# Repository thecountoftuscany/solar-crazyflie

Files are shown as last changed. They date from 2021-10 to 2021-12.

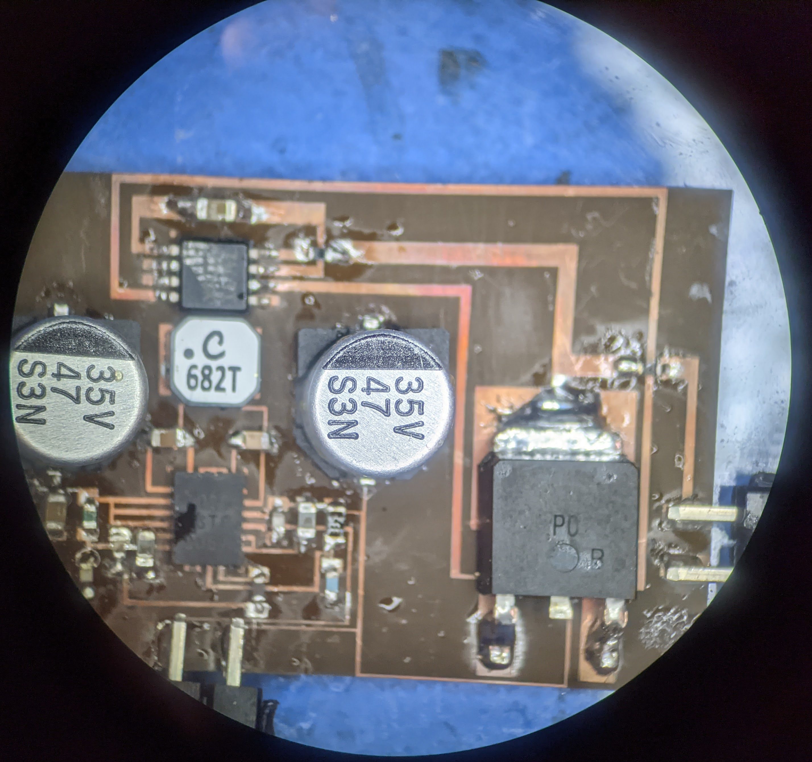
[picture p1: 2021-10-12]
resources/ckt_cropped.jpg

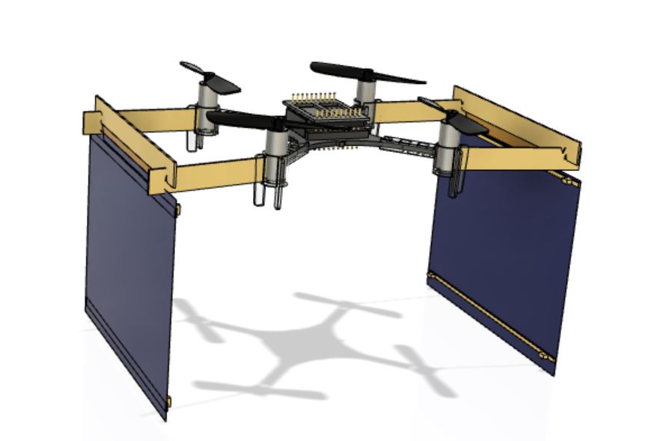
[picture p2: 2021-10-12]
resources/solar-panels-retracted.JPG

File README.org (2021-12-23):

#+title: Toward battery-free flight: Duty cycled recharging of small drones (IEEE IROS 2021)
#+author: Nishant Elkunchwar, Suvesha Chandrasekaran, Vikram Iyer, Sawyer B. Fuller

This repository contains the source code and circuit schematics used in the IEEE IROS 2021 paper titled [[https://ieeexplore.ieee.org/document/9636087][Toward battery-free flight: Duty cycled recharging of small drones]].
#+html: <p align="center"><img src="resources/drone.JPG" alt="The drone carrying the thin film solar panels and all other components" width="500" /></p>

* Major highlights
** A solar charging circuit
#+html: <p align="center"><img src="resources/ckt_cropped.jpg" alt="Solar charging circuit" width="500" /></p>
- 39 x 21 mm, 1.83 g circuit laser etched using a DPSS laser machine
- 90.84 % average efficiency across different light intensities (see the [[Results]] section)
- charges a 250 mAh 1S LiPo battery completely with two 94 x 73 mm (1.98 g each) thin film flexible solar panels in 3 hr 3 min (see the [[Results]] section) in real outdoor lighting varying due to intermittent clouds
** A passive folding mounting mechanism
https://user-images.githubusercontent.com/14308382/136243970-1dca0429-ac65-4f95-9dc4-829e8c846ea5.mp4
- fabricated using 2.3 mm balsa wood, weighs just 0.83 g
- enables airflow from propellers for lift, decreases destabilizing torques
- uses gravity for folding down and ground effect (increase in air pressure below the drone near the ground) to open out the panels; passive mechanism implies no actuators, making it simple, effective and light
** A landing site selection strategy
https://user-images.githubusercontent.com/14308382/136245977-f141101d-2a0c-4fd0-a3ba-4daf73d85fbe.mov
- detects presence of light to avoid landing in shaded regions
- avoids crashing into nearby obstacles
- avoids landing in unflat terrain where panels cannot open out for recharging
* Description of repository contents
- [[./circuits][circuits]]: charging circuit schematics and vector drawings used for laser etching
- [[./data][data]]: all recorded experiment data used for generating all plots (see the [[Results]] section)
- [[./docs][docs]]: relevant datasheets etc
- [[./resources][resources]]: resources used in this README
- [[./scripts][scripts]]: all scripts
  - [[./scripts/plots][scripts/plots]]: the scripts used for generating all plots (see the [[Results]] section)
  - [[./scripts/controller.py][scripts/controller.py]]: script used to manually control the crazyflie and trigger the landing site selection sequence. Heavily borrows from [[https://github.com/thecountoftuscany/crazyflie-run-and-tumble/blob/master/scripts/cflibController.py][thecountoftuscany/crazyflie-run-and-tumble/scripts/cflibController.py]] for the keyboard control part.
    - While the battery is not low, the drone is controlled manually to fly around. This behaviour can be substituted with whatever persistent operations (autonomous or otherwise) are desired in a particular application.
    - To get outside a shaded area, the drone keeps moving forward (defined as at least 1000 lux for indoor light, and 100,000 lux for outdoors). This behaviour can be changed to a random walk or anything else as desired.
    - To avoid obstacles, the drone moves directly away from the closest one. This behaviour can be changed to turning away, wall-following, sliding mode controller or anything else as desired
    - On detecting an unflat area, the drone moves forward by a set amount to re-check for flatness. This behaviour can be changed to a random walk or anything else as desired
    - To check for flatness, the drone measures time of flight measurements while moving in a square around the area to be tested. This behaviour can be changed to a different trajectory (for eg. a circle) as desired.
  - [[./scripts/crazyflie-thrust-control.py][scripts/crazyflie-thrust-control.py]]: script used to control crazyflie's thrust (open loop, constant or closed loop, hovering) and save data for flight performance plots (see the [[Results]] section)
* Requirements
The following python packages (obtain using =pip=, =conda=, your OS distribution package manager or any other preferred means):
- =numpy=
- =pygame=
- [[https://github.com/bitcraze/crazyflie-lib-python][cflib]]
- =argparse=
- =matplotlib=
* Background
** UAV flight time limits persistent operations
- Battery capacity limits flight time: low energy density of currently available batteries, but high power required for hovering flight
- Miniaturization reduces required flight power and solar harvesting increases flight time
** Why solar power?
*** Scaling effects due to miniaturization
#+html: <p align="center"><img src="resources/mass_vs_array_scaling2.png" alt="PV cell size required for hovering reduces faster than drone size" width="500" /></p>
- Scaling effects lead to lower required hover power for smaller robots. This scales down faster than required photovoltaic panel size required for continuous hover (see figure).
- For scale l:
  + PV cell area scales as l^2
  + Required flight power for hovering scales as l^7/2
- From existing robots, we can see this trend that required PV cell size for continuous hovering becomes smaller than the robot size below approx 1 g robot mass. For robots slightly above this threshold duty cycled operation is possible: that is, the robot operates normally until the battery is low, at which point it stops, recharges its battery and continues operation indefinitely.
*** Simplicity: previous solutions too complicated for small aerial robots
+ Tethered flight: restricts drone movement
+ Wireless power transfer, autonomously docking to power outlets, hot-swapping UAV batteries in-flight: needs additional base stations or docks, bulky sensors (eg. cameras, lidars) to search for and align / dock with them, computationally intensive algorithms (eg. computer vision) for planning, and additional sensors for localization. Also restricts how far the drone can travel via dependence on these external systems
+ Solar-powered hovering for fixed wing drones: only achieved on large, fixed wing drones. Large size increases cost, use of unpackaged monocrystalline solar panels makes them fragile, and being fixed wing decreases agility and they cannot hover which limits their utility for many applications
In contrast, this system is simple, self-contained and deployable on size, weight, power and computationally limited platforms, specially, insect scale robots like the [[https://arxiv.org/pdf/2001.02320.pdf][UW Robofly]].
** Why duty cycled?
- Inspiration from IoT radios: low average power
- Continuous hover with only solar power not possible at this scale. Duty cycled operation enables indefinite operation without any human intervention or existence of any external power infrastructure.
- Traversal of long distances possible: no need for a return journey
* System
- 21 g palm-sized drone, Crazyflie 2.1 with optic flow deck, multiranger deck, and BH1750 light sensor (driver can be obtained [[https://github.com/thecountoftuscany/crazyflie-run-and-tumble/blob/master/crazyflie-firmware/src/deck/drivers/src/bh1750deck.c][here]])
- Custom charging circuit
#+html: <p align="center"><img src="resources/schematic.png" alt="Charging circuit schematic" width="500" /></p>
- Solar panels: two thin-film flexible, amorphous silicon cells (200 microns), 94 x 73 mm
* Results
** Solar charging
*** Complete battery charge
#+html: <p align="center"><img src="resources/charging-curve.png" alt="Solar charging a LiPo battery" width="500" /></p>
*** Charging efficiency
#+html: <p align="center"><img src="resources/efficiency.png" alt="Efficiency of charging circuit" width="400" /></p>
*** Charging times for different cell configurations
|----------------+----------+---------------------------------+----------------+---------------------|
| Panels         | Mass (g) | Avg light intensity (x10^3 lux) | Avg efficiency | Charging time (min) |
|----------------+----------+---------------------------------+----------------+---------------------|
| two MPT4.8-75  |     3.96 |                          107.16 |         90.84% |                 183 |
| four MPT4.8-75 |     7.92 |                           71.41 |         89.61% |                  84 |
| four MPT6-75   |     9.20 |                           65.74 |          86.94 |                  80 |
|----------------+----------+---------------------------------+----------------+---------------------|
** Folding solar panel mounts
#+html: <p align="center"><img src="resources/solar-panels-flat.png" alt="Battery discharge curves under different loads" width="320" /> <img src="resources/solar-panels-retracted.JPG" width="320"></p>
*** Necessity
- to allow airflow from propellers
- to reduce imbalancing torques
- to enable passive transition between states
*** Flight performance
- 4.7 min flight time
- can travel 400 m at maximum velocity in single discharge, or 1.2 km in a day (assuming two recharges which is typical in a day)
#+html: <p align="center"><img src="resources/discharging-curves.png" alt="Battery discharge curves under different loads" width="320" /></p>
** Landing site selection
#+html: <p align="center"><img src="resources/flatness-check-colored.png" alt="Landing site selection algorithm" width="800" /></p>
* Authors
For more details refer to the paper [[https://ieeexplore.ieee.org/document/9636087][here]]. You can also contact one of the authors below:
- [[https://students.washington.edu/nishante][Nishant Elkunchwar]]
- [[https://www.linkedin.com/in/suvesha-c][Suvesha Chandrasekaran]]
- [[https://homes.cs.washington.edu/~vsiyer/][Vikram Iyer]]
- [[https://faculty.washington.edu/minster/][Sawyer B. Fuller]]
* Acknowledgements
The authors would like to thank [[https://yogeshchukewad.com/][Yogesh Chukewad]] for insightful suggestions during the writing of the paper, and [[https://www.afrl.af.mil/AFOSR/][The Air Force Office of Scientific Research (AFOSR)]], grant no. FA9550-14-1-0398 by [[http://nifti.washington.edu/][The Air Force Center of Excellence on Nature-Inspired Flight Technologies and Ideas (NIFTI)]] for funding the equipment used in this research.

* Todos
- [ ] The crazyflie now has an [[https://www.bitcraze.io/documentation/repository/crazyflie-firmware/2020.02/app_layer/][app layer]]. Implement this algorithm on-board and remove the dependency on an external computer

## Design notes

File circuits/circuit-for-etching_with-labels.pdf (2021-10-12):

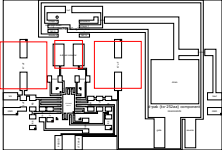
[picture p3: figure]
LTC3130; GND 21; BST1 1; PVIN 2; VIN 3; RUN 4; VCC 5; MPPC 6; GND 7; GND 8; ILIM 10; MODE 11; EXTVcc 12; PGOOD 13; VOUT 14; BST2 16; PGND 19; PGND 18; 6.8 uH inductor; Vin; GND; 0 ohm; Vout; PGOOD; LTC Vout; VCapL 1 Gate pull down 2 NC 3; Anode 4; Gate drive 6; VCapH 7; Cathode 8; d-pak (to-252aa) component; IRLR024NTR; drain; gate; source

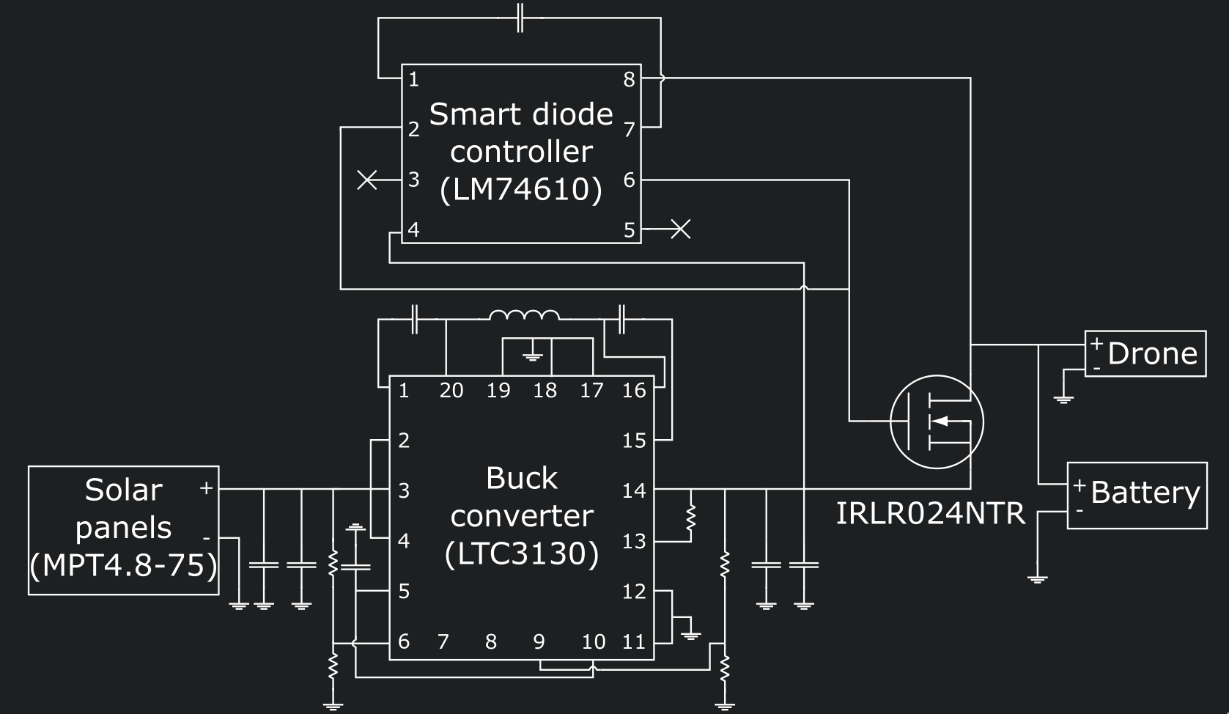
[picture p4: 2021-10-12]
resources/schematic.png

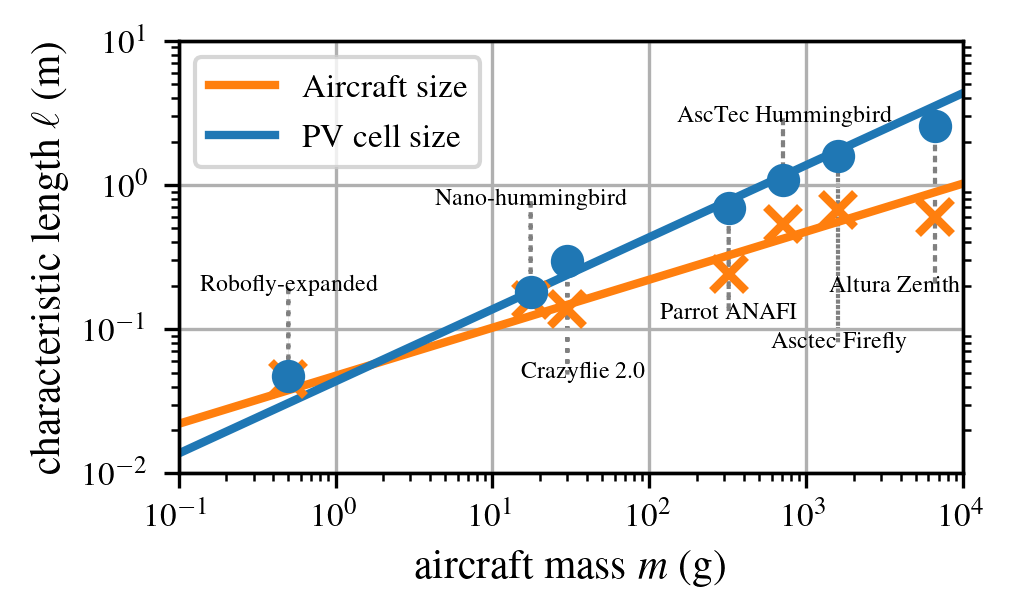
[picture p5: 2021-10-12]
resources/mass_vs_array_scaling2.png

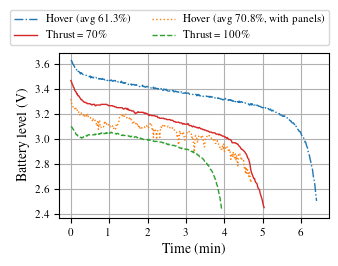
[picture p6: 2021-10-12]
resources/discharging-curves.png

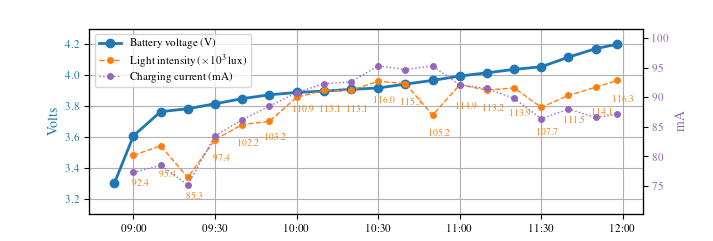
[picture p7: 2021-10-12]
resources/charging-curve.png

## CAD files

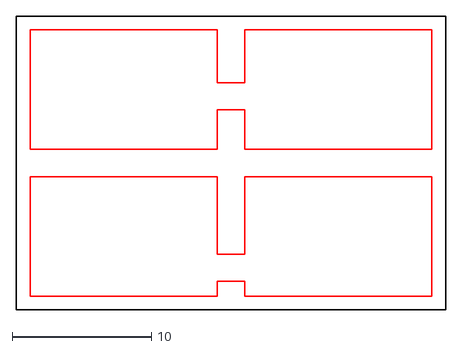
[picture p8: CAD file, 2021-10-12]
circuits/etching/dxf/fr4.dxf
30.8 x 21.1

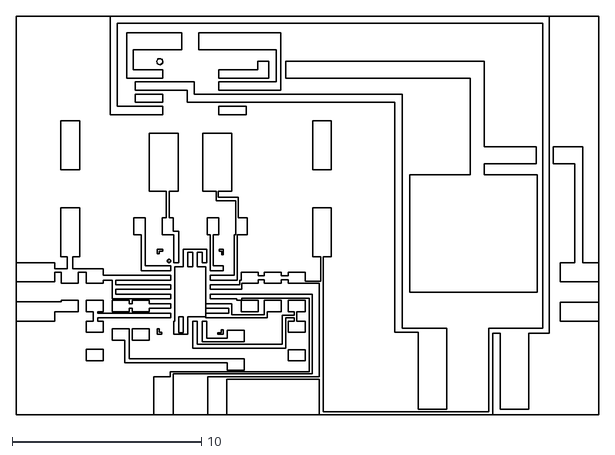
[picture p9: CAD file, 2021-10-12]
circuits/etching/dxf/drawing+bb.dxf
30.8 x 21.1

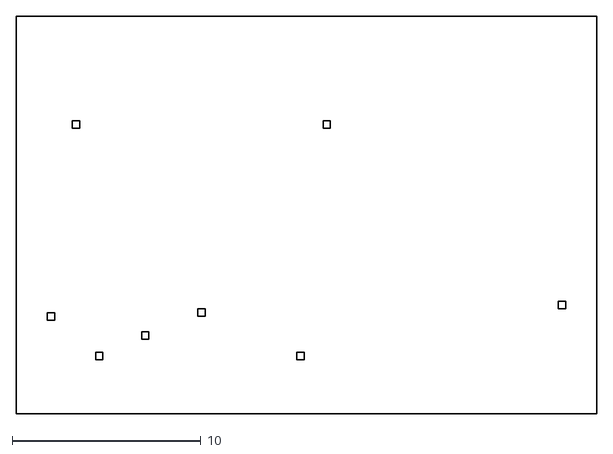
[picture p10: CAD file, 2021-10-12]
circuits/etching/dxf/bb+gnd.dxf
30.8 x 21.1
